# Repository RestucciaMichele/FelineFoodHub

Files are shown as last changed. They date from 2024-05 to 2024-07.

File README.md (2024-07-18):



Progetto creato per il corso di [Sistemi Embedded](https://gitlab.di.unimi.it/sistemiembedded) dell'Università Statale di Milano
_______________________________
### hardware utilizzato
  - **board**:
    - [STMicroelectronics STM32-F401RE](https://www.st.com/en/evaluation-tools/nucleo-f401re.html)
  - **attuatori**:
    - [led rgb](https://www.amazon.it/Youmile-emissione-Tri-Color-trasparenti-potrebbero/dp/B0897L6TZ8)
    - [servomotore](https://www.amazon.it/Aihasd-28YBJ-48-4-Phase-Stepper-Arduino/dp/B00U744GJU)
  - **sensori**:
    - [pulsante con leva](https://www.amazon.it/GOLRISEN-Interruttore-Finecorsa-Attuatore-Momentaneo/dp/B07F9QKTQQ)
    - [sensore di distanza a ultrasuoni](https://www.amazon.it/CML-Modulo-Ultrasuoni-Distanza-Trasduttore-Misurazione/dp/B00JB1C142)
    - [cella di carico (1 kg)](https://www.amazon.it/elettronica-portatile-sensore-HX711-pesatura-Raspberry/dp/B076PYX5DW)

### funzionamento in breve
Il progetto prevede la realizzazione di un distributore di croccantini che, durante l'arco della giornata, riempia la ciotola del cibo in modo autonomo. Il sistema utilizza una cella di carico per registrare il peso del cibo presente nella ciotola e attivare un servomotore quando necessario, garantendo così un rifornimento costante. Inoltre, un sensore di distanza a ultrasuoni controlla il livello di croccantini nel contenitore, segnalando quando la riserva sta per esaurirsi.  
Il led RGB segnala diversi stati:
  - **in blu**, il contenitore non ha più abbastanza cibo da fornire
  - **in rosso**, il coperchio del contenitore è aperto per ricaricare la scorta di croccantini (in questa fase tutto il sistema è momentaneamente sospeso)
  - **in verde**, il servomotore sta fornendo cibo
_______________________________
### costruzione
- questo è lo schema del plexiglass (da 4 mm) da tagliare, con tutte le misure che ho usato per costruire la struttura. Successivamente con una pistola termica ho modellato il plexiglass creando delle curve di 90° per ogni lato da piegare.
  <br><br>misure plexiglass<br><br>
  **1° N.B.** le proporzioni nell'immagine non sono quelle reali. Serve solo per avere le indicazioni sulle misure<br>
  **2° N.B.** i fori segnati servono per non crepare il plexiglass durante la piegatura    </td>
  
- successivamente ho creato e stampato, con filamento PLA, degli oggetti 3d per completare le parti mancanti:  
  - il [coperchio](https://github.com/RestucciaMichele/FelineFoodHub/blob/main/readmeFiles/coperchio.stl) (che ospita il pulsante e il sensore di distanza a ultrasuoni)
  - il [piatto](https://github.com/RestucciaMichele/FelineFoodHub/blob/main/readmeFiles/distributore.stl) che fa anche da distributore (al quale viene fissata tutta l'elettronica principale)
  - tre [passacavi](https://github.com/RestucciaMichele/FelineFoodHub/blob/main/readmeFiles/passacavi.stl) (per tenere la struttura in plexiglass rigida e per non fare vedere i cavi passanti dal coperchio al distributore)
  - altri tipi di [viti](https://github.com/RestucciaMichele/FelineFoodHub/blob/main/readmeFiles/VITI.stl) (che migliorano l'erogazione dei croccantini)

### prototipo
<table>
  <tr>
    <td>
      prototipo
    </td>
    <td>
      circuito
    </td>
  </tr>
</table>

________________________
### errori
- cavi troppo corti
- motorino troppo debole
- piatto distributore poco inclinato

### possibili miglioramenti futuri
lato programmazione:
- migliorare lettura codice tramite, prototipo della funzione (per togliere i task in mezzo al codice)
- inserire funzioni anonime per limitare numero di prototipi della funzione (led rgb task)
- eliminare delay microsecond con libreria interrupt per sensore ad ultrasuoni di distanza
- schedulare anche lo stepper (prima task avanti, all'ultimo passo inserire task indietro)

in futuro si potrebbe migliorare il progetto, inserendo:
- un motorino dc che, vibrando, non faccia bloccare i croccantini nel contenitore
- un sensore per identificare quando c'è un gatto in avvicinamento, così da non far partire nessun attuatore e farlo mangiare senza distrazioni.
- algoritmo che proporzioni il cibo dato durante la giornata rispetto ad una quantità massima decisa dall'utente
- un collegamento al wifi per:
  - memorizzare in un giorno la quantità di cibo mangiato o altre informazioni
  - notificare all'utente informazioni, tra cui quanto ha mangiato il gatto o se sta per finire il cibo
- un display per gestire tutte le informazioni di setup iniziali e visualizzare gli stati in cui è il distributore durante l'arco delle giornate.

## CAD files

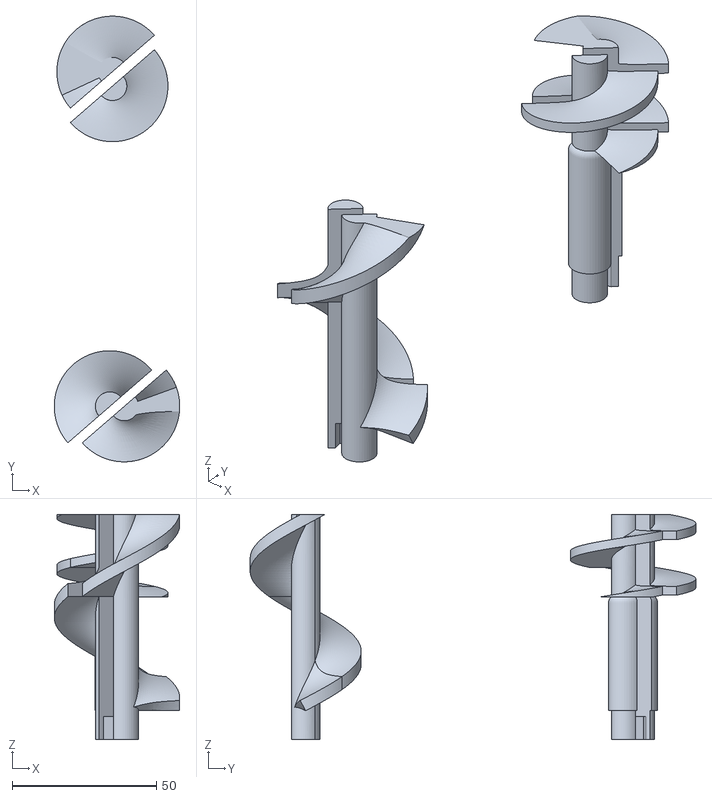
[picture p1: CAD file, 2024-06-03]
readmeFiles/VITI.stl
43.5 x 154.5 x 78.0

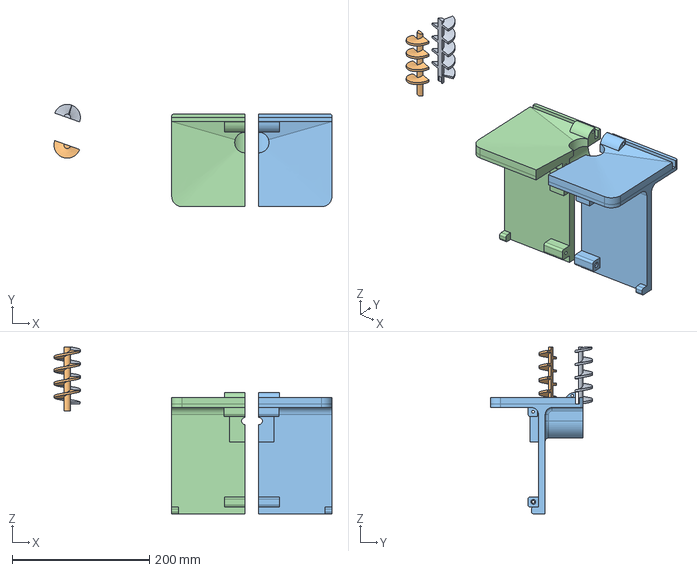
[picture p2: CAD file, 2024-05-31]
readmeFiles/distributore.step
405.2 x 149.1 x 243.2 mm
piatto
VITE v3

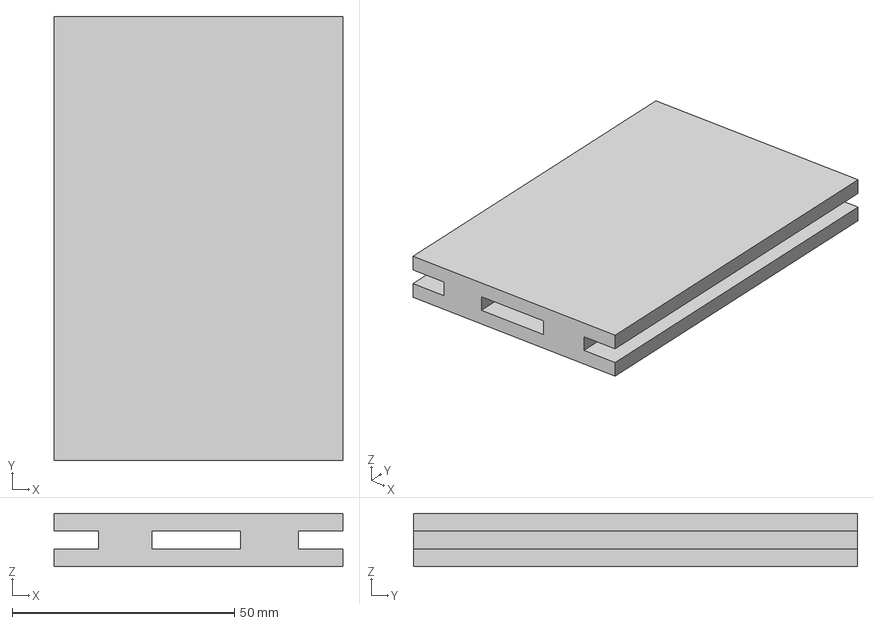
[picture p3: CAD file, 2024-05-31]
readmeFiles/passacavi.step
65.0 x 100.0 x 12.0 mm

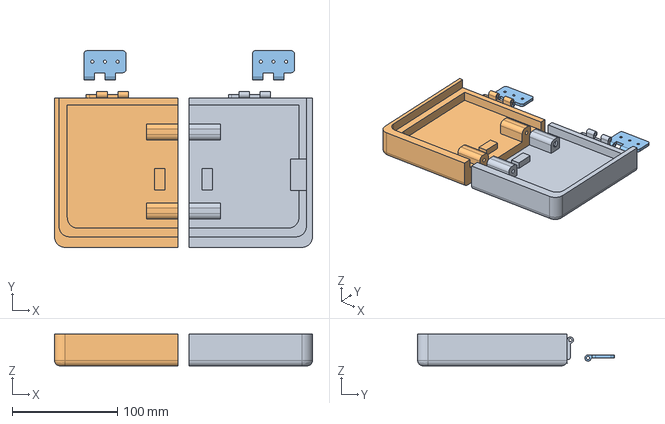
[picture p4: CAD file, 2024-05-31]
readmeFiles/coperchio.step
245.0 x 186.8 x 30.0 mm
Componente2
Componente3 x 2

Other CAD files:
readmeFiles/coperchio.stl
readmeFiles/distributore.stl
readmeFiles/passacavi.stl

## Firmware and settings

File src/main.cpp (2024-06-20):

#include <Arduino.h>
#include <TaskScheduler.h>
#include <Stepper.h>
#include <HX711.h>  //https://github.com/bogde/HX711 non è una libreria che si trova dalle risorse di Arduino IDE
#include <StopWatch.h>


#define _TASK_SLEEP_ON_IDLE_RUN
#define _TASK_STATUS_REQUEST

// ======= PIN =======
const int echoPin = 2;    // Echo pin for ultrasonic sensor
const int triggerPin = 3;  // Trigger pin for ultrasonic sensor
const int LOADCELL_SCK_PIN = 4;
const int LOADCELL_DOUT_PIN = 5;  
const int rgbPins[] = {6, 7, 8}; // red, green, blue
const int motorPin1 = 9;  // IN1 on the ULN2003 driver
const int motorPin2 = 10;  // IN3 on the ULN2003 driver
const int motorPin3 = 11;  // IN2 on the ULN2003 driver
const int motorPin4 = 12;  // IN4 on the ULN2003 driver
const int buttonPin = 13;

// ======= VARIABILI GLOBALI =======
const int intervalloControlloCiotola = 30; // secondi
const int intervalloCoperchio = 1; // secondi

const int distanzaContenitoreVuoto = 17; // cm
float distanzaDalCibo;

const int giriVite = 20;  // 20 per un giro completo

const int pesoCiboMinimo = 15;
const int pesoCiboMassimo = 60;
const float calibrationLoadCell = 2076.89; // valore per la prima calibrazione iniziale all'accensione
float calibrationDrift = calibrationLoadCell;
float pesoAttuale;

// ======= MOTORE STEPPER =======
const int stepsPerRevolution = 2048;  // 1 giro = 2048 passi
Stepper stepper = Stepper(stepsPerRevolution, motorPin1, motorPin3, motorPin2, motorPin4);
void stepperMove(int step) {
  stepper.setSpeed(14);
  stepper.step(step);
}

void moveForward() {
  stepperMove(200);
  stepperMove(-100);
}

// ======= BILANCIA, LOAD CELL =======
HX711 scale;
StopWatch timer;
void misuraPeso() {
  scale.power_up();
  
  timer.stop();
  calibrationDrift = calibrationDrift + ((timer.elapsed() / 300000) * 0.001 ); // ogni 5 minuti = 300000 millis, aggiorno la calibrazione
  timer.reset();
  timer.start();
  
  scale.set_scale(calibrationDrift);
  pesoAttuale = scale.get_units(10);

  scale.power_down();
}

// ======= DISTANZA ULTRASUONI =======
long durata;
void misurazioneDistanza() {
  digitalWrite(triggerPin, LOW);  // gli impulsi LOW servono per pulire il segnale per la ricezione del vero impulso HIGH di 10 microsecondi
  delayMicroseconds(5);           // delay obbligatori per il corretto funzionamento del sensore
  digitalWrite(triggerPin, HIGH);
  delayMicroseconds(10);
  digitalWrite(triggerPin, LOW);

  durata = pulseIn(echoPin, HIGH);
  
  distanzaDalCibo = (durata/2.0 * 0.0343); // cm
}

// ================= FADE LED RGB =================
void setColor(int redValue, int greenValue, int blueValue) {
  analogWrite(rgbPins[0], redValue);
  analogWrite(rgbPins[1], greenValue);
  analogWrite(rgbPins[2], blueValue);
}

int brightness = 0;
int fadeAmount = 5;
void ledFade(String Color) {
  if (Color == "red") {
    setColor(brightness, 0, 0);
  } else if (Color == "blue") {
    setColor(0, 0, brightness);
  } else {
    setColor(0,0,0);
  }

  brightness = brightness + fadeAmount;

  if (brightness <= 0 || brightness >= 255) {
    fadeAmount = -fadeAmount;
  }
}

// ================== TASK SETUP ==================
void controlloAperturaCoperchio();
void controlloCiotola();
void ledFadeRed() {ledFade("red");}
void ledFadeBlue() {ledFade("blue");}
void Motore();
Scheduler runner;
Task TaskLedRed(30*TASK_MILLISECOND, TASK_FOREVER, &ledFadeRed);
Task TaskLedBlue(30*TASK_MILLISECOND, TASK_FOREVER, &ledFadeBlue);
Task TaskControlloAperturaCoperchio(intervalloCoperchio*TASK_SECOND, TASK_FOREVER, &controlloAperturaCoperchio);
Task TaskAttivazioneMotore(TASK_MILLISECOND, giriVite, &Motore);
Task TaskControlloCiotola(intervalloControlloCiotola*TASK_SECOND, TASK_FOREVER, &controlloCiotola);

// ================== APERTURA COPERCHIO ==================
void resetLed() { // funzione chiamata tramite la funzione controlloAperturaCoperchio, schedulata ogni secondo. In questo modo il led non rimane acceso dall'ultima chiamata di ledFade
  if (!TaskLedRed.isEnabled() && !TaskLedBlue.isEnabled()) {
    brightness = 0;
    fadeAmount = 5;
    ledFade("red"); // va bene qualsiasi colore
  }
}

void controlloAperturaCoperchio() {
  if (digitalRead(buttonPin)==LOW) {  // coperchio aperto -> disabilito tutti i task
    Serial.println(F("COPERCHIO APERTO. Disabilitazione task ..."));
    TaskAttivazioneMotore.disable();
    TaskControlloCiotola.disable();
    TaskLedBlue.disable();
    TaskLedRed.enableIfNot();
  } else {            // coperchio chiuso -> disabilito task led e abilito i gli altri task
    TaskLedRed.disable();
    resetLed();       //controllo funziona per tutte le chiamate di led (anche per colori diversi), quindi basta questo
    TaskControlloCiotola.enableIfNot();
  }
}

// ================== CONTROLLO BILANCIA E MOTORE CIOTOLA==================
void Motore() {
  setColor(0,255,0);
  moveForward();
  setColor(0,0,0);
}

bool ricaricato = false;
void controlloCiotola() {
  Serial.print(F("controllo quantità scorta di cibo ==> "));
  misurazioneDistanza();
  Serial.println(distanzaDalCibo);
  if (distanzaDalCibo >= distanzaContenitoreVuoto) {
    Serial.println(F("SCORTA INSUFFICIENTE. ricarica di cibo non possibile ..."));
    TaskLedBlue.enableIfNot();
  } else {
    TaskLedBlue.disable();
    Serial.print(F("SCORTA SUFFICIENTE. controllo quantità cibo nella ciotola ==> "));
    misuraPeso();
    Serial.println(pesoAttuale);
    if (pesoAttuale < pesoCiboMinimo || ricaricato == true) {
      Serial.println(F("CIBO INSUFFICIENTE. Attivazione motore ..."));
      TaskAttivazioneMotore.restart();
      ricaricato = true;
      if (pesoAttuale >= pesoCiboMassimo) {
        Serial.println(F("CIBO SUFFICIENTE. Motore non attivato"));
        ricaricato = false;
        TaskAttivazioneMotore.disable();
      }
    } else {
      Serial.println(F("CIBO SUFFICIENTE. Motore non attivato"));
    }
  }
}

// ================== SETUP ==================
void schedulerSetup() {
  runner.init();

  runner.addTask(TaskLedRed);
  runner.addTask(TaskLedBlue);
  runner.addTask(TaskControlloAperturaCoperchio);
  runner.addTask(TaskAttivazioneMotore);
  runner.addTask(TaskControlloCiotola);
  
  TaskControlloAperturaCoperchio.enable(); 
  TaskControlloCiotola.enable();
}

void loadCellSetup() {
  scale.begin(LOADCELL_DOUT_PIN, LOADCELL_SCK_PIN);
  scale.set_scale();
  scale.tare();
  scale.power_down();

  timer.start();  // avvio il cronometro per la calibrazione continua della bilancia
}

void initialSetup() {
  Serial.println(F("Inizializzazione dispositivo FelineFoodHub ..."));
  delay(2000);
  Serial.println(F("appoggiare sopra la bilancia una ciotola vuota per la calibrazione e taratura ..."));
  delay(2000); Serial.println(F("..."));
  delay(2000); Serial.println(F("..."));
  delay(2000); Serial.println(F("..."));
  Serial.println(F("Inizio Calibrazione ..."));
  loadCellSetup();
  Serial.println(F("Calibrazione completata. Bilancia pronta per l'uso ..."));
  schedulerSetup();
}

void setup() {
  Serial.begin(9600);

  pinMode(rgbPins[0], OUTPUT);  //red
  pinMode(rgbPins[1], OUTPUT);  //green
  pinMode(rgbPins[2], OUTPUT);  //blue
  pinMode(buttonPin, INPUT_PULLUP);  //bottone apertura coperchio
  pinMode(triggerPin, OUTPUT);  //ultrasonic
  pinMode(echoPin, INPUT);      //ultrasonic

  initialSetup();
}

void loop() {
  runner.execute();
}

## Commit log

2024-05-15 inserimento sensore ultrasuoni
2024-06-02 aggiunta cella di carico e stepper
2024-06-03 versioni diverse viti
    [VITI.stl]
2024-06-03 tipologie diverse di viti
    [VITI.stl]
2024-06-06 gestione drift valore di calibrazione
2024-06-07 modifica Serial.print()
2024-06-14 rename folder
    [VITI.stl, coperchio.step, coperchio.stl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]
